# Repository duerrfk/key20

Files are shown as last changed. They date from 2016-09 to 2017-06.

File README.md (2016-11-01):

# What is Key 2.0?

Key 2.0 (or Key20 for short) is a Bluetooth IoT Door Lock controller. It turns a conventional electric door lock into a smart door lock that can be opened using a smartphone without the need for a physical key. Thus, Key20 is the modern version of a physical key, or, as the name suggests, the key version 2.0 for the Internet of Things (IoT) era.

Key20 consists of two parts:

1. Key20 door lock controller device, which is physically connected to the electric door lock and wirelessly via BLE to the mobile app.
2. Key20 mobile app implementing the user interface to unlock the door and communicating with the door lock controller through BLE.

```
         [ Mobile Phone w/ ]
         [    Key20 App    ]
               |
               | Bluetooth Low Energy (BLE) Connection
               |
 |---[ Key20 Door Lock Controller ]---[ Electric Door Lock ]---|
 |   [           Device           ]                            |
 |                                                             |
 |                                                             |
 |                                                             |
 |----------------------(Voltage Source)-----------------------|
                        (    12 VAC    )
```

The following image shows the Key20 door lock controller device and the Key20 app running on a smartphone.

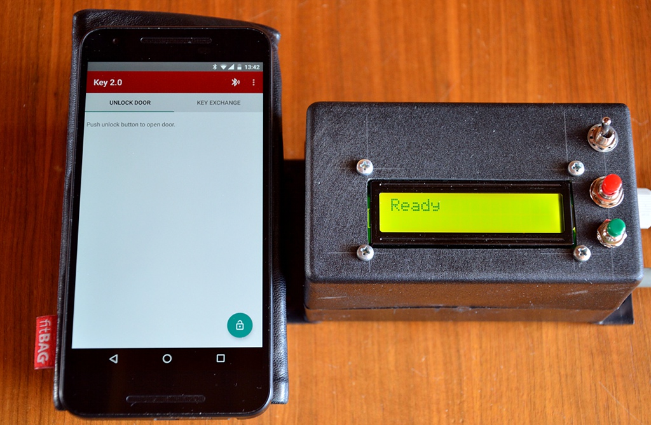
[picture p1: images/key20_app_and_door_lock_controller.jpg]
Key 2.0 Door Lock Controller and App


You can get a quick impression on how Key20 works watching the following video:

[Key 2.0 Video](https://youtu.be/0vUUZOasrV8)

The main features of Key20 are:

* Using state-of-the-art security mechanisms (Elliptic Curve Diffie-Hellman Key Exchange (ECDH), HMAC) to protect against attacks. 
* Open-source software and hardware, including an open implementation of the security mechanisms. No security by obscurity! Source code for the app and door lock controller as well as Eagle files (schematic and board layout) are provided.
* Maker-friendly: using easily available cheap standard components (nRF51822 BLE chip, standard electronic parts), easy to manufacture circuit board, and open-source software and hardware design.
* Works with BLE-enabled Android 4.3 mobile devices (and of course newer versions). Porting to other mobile operating systems like iOS should be straightforward.
* Liberal licensing of software and hardware under the Apache License 2.0 and the CERN Open Hardware License 1.0, respectively.

# Security Concepts

A door lock obviously requires security mechanisms to protect from unauthorized requests to open the door. To this end, Key20 implements the following state of the art security mechanisms.

## Authorization of Door Open Requests with HMAC

All door open requests are authorized through a Keyed Hash Message Authentication Code (HMAC). A 16 byte nonce (big random number) is generated by the door lock controller for each door open request as soon as a BLE connection is made to the door lock controller. The nonce is sent to the mobile app. Both, the nonce and the shared secret, are used by the mobile app to calculate a 512 bit HMAC using the SHA-2 hashing algorithm, which is then truncated to 256 bits (HMAC512-256), and sent to the door lock controller. The door lock controller also calculates an HMAC based on the nonce and the shared secret, and only if both HMACs match, the door will be opened. 

The nonce is only valid for one door open request and effectively prevents replay attacks, i.e., an attacker sniffing on the radio channel and replaying the sniffed HMAC later. Note that the BLE radio communication is not encrypted, and it actually does not need to be encrypted since a captured HMAC is useless when re-played. 

Moreover, each nonce is only valid for 15 s to prevent man-in-the-middle attacks where an attacker intercepts the HMAC and does not forward it immediatelly but waits until the (authorized) user walks away after he is not able to open the door. Later the attacker would then send the HMAC to the door lock controller to open the door. With a time window of only 15 s (which could be reduced further), such attacks are futile since the authorized user will still be at the door.

Note that the whole authentication procedure does not include heavy-weight asymmetric crypto functions, but only light-weight hashing algorithms, which can be performed on the door lock device featuring an nRF51822 micro-controller (ARM Cortex M0) very fast in order not to delay door unlocking. 

With respect to the random nonce we would like to note the following. First, the nRF51822 chip includes a random number generator for generating random numbers from thermal noise, so nonces should be of high quality, i.e., truly random. An attack by cooling down the Bluetooth chip to reduce randomness due to thermal noise is not relevant here since this requires physical access to the lock controller installed within the building, i.e., the attacker is then already in your house.

Secondly, 128 bit nonces provide reasonable security for our purpose. Assume one door open request per millisecond (very pessimistic assumption!) and 100 years of operation, i.e., less than n = 2^42 requests to be protected. With 128 bit nonces, we have m = 2^128 possible nonce values. Then the birthday paradox can be used to calculate the probability p of at least one pair of requests sharing the same nonce, or, inversely, no nonces shared by any pair of requests. An approximation of p for n << m is p(n,m) = 1 - e^((-n^2)/(2*m)), which practically evaluates to 0 for n = 2^42 and m = 2^128. Even for n = 2^52 (one request per us; actually not possible with BLE), p(2^52,2^128) < 3e-8, which is about the probability to be hit by lightning, which is about 5.5e-8.

## Exchanging Keys with Elliptic Curve Diffie Hellman Key Exchange (ECDH)

Obviously, the critical part is the establishment of a shared secret between the door lock controller and the mobile app. Anybody in possession of the shared secret can enter the building, thus, we must ensure that only the lock controller and the Key20 app know the secret. To this end, we use Elliptic Curve Diffie-Hellman (ECDH) key exchange based on Curve 25519. We assume that the door lock controller is installed inside the building that is secured by the lock---if the attacker is already in your home, the door lock is futile anyway. Thus, only the authorized user (owner of the building) has physical access to the door lock controller. 

First, the user needs to press a button on the door lock controller device to enter key exchange mode (the red button in the pictures). Then both, the mobile app and the door lock controller calculate different key pairs based on the Elliptic Curve 25519 and exchange their public keys, which anyone can know. Using the public key of the other party and their own private keys, the lock controller and the app can calculate the same shared secret. 

Using Curve 25519 and the Curve 25519 assembler implementation optimized for ARM Cortex-M0 from the Micro NaCl project, key pairs and shared secrets can be calculated in sub-seconds on the nRF51822 BLE chip (ARM Cortex M0). 

Without further measures, DH is susceptible to man-in-the-middle attacks where an attacker actively manipulates the communication between mobile app and door lock controller. With such attacks, the attacker could exchange his own public key with both, the lock controller and the app to establish two shared secrets between him and the door lock controller, and between him and the mobile app. We prevent such attacks with the following mechanism. After key exchange, the mobile app and the door lock device both display a checksum (hash) of their version of the exchanged shared secret. The user will visually check these checksums to verify that they are the same. If they are the same, no man-in-the-middle attack has happened since the man in the middle cannot calculate the same shared secret as the door lock controller and the mobile app (after all, the private keys of door lock controller and mobile app remain private). Only then the user will confirm the key by pressing buttons on the door lock controller and the mobile app. Remember that only the authorized user has physical access to the door lock controller since it is installed within the building to be secured by the lock. 

The following image shows the mobile app and the door lock controller displaying a shared secret checksum after key exchange. The user can confirm this secret by pushing the green button the the lock controller device and the Confirm Key button of the app.

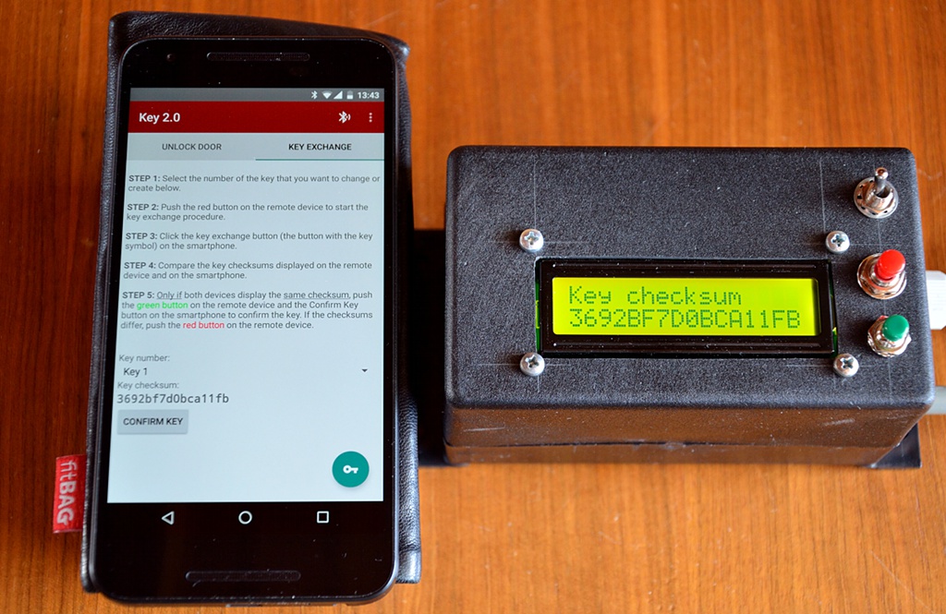
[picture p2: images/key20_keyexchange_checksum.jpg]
Key Exchange with Checksum

 
## Why not Standard Bluetooth Security?

Actually, Bluetooth 4.2 implements security concepts similar to the mechanisms described above. So it is a valid question why don't we just rely on the security concepts implemented by Bluetooth?

A good overview why Bluetooth might not be as secure as we would like it to be is provided by [Francisco Corella](https://pomcor.com/2015/06/03/has-bluetooth-become-secure/). So we refer the interested reader to his page for the technical details and a discussion of Bluetooth security. We also would like to add that many mobile devices still do not implement Bluetooth 4.2 but only Bluetooth 4.0, which is even less secure than Bluetooth 4.2.

So we decided not to rely on Bluetooth security mechanisms, but rather implement all security protocols on the application layer using state of the art security mechanisms as described above.

# Bluetooth Door Lock Controller Device

The Door Lock Controller Device needs to be connected to the electric door lock (2 cables). You can simply replace a manual switch by the door lock controller device. 

The door lock controller needs to be placed in Bluetooth radio range to the door and inside the building. Typical radio ranges are about 10 m. Depending on the walls, the distance might be shorter or longer. In our experience, one concrete wall is no problem, but two might block the radio signal.  

## Door Lock Controller Hardware

The door lock controller hardware is designed for operating AC (alternating current) electric door locks, which typically run from 6-12 VAC. 

The hardware design (schematics and board layout for Eagle) for the door lock controller device can be found in folder `pcb/key20-ble`. 

The following images show the hardware and schematic. The hardware basically concists of one circuit board (PCB). We deliberately used a simple single-sided through-hole design to help makers producing their own boards. An LCD, a power switch, and two push buttons for user interaction are connected to the main PCB. An ob-board voltage regulator provides 3.3 V fed by an external DC power supply (anything between 4 V and 30 V will work). The circuit draws less than 50 mA when the lock is operated, thus, you can use a cheap 5.0 V USB power supply. With a little modification, we could also switch off the LCD when not needed, and the device could run from 4 AA-size batteries most probably for years.

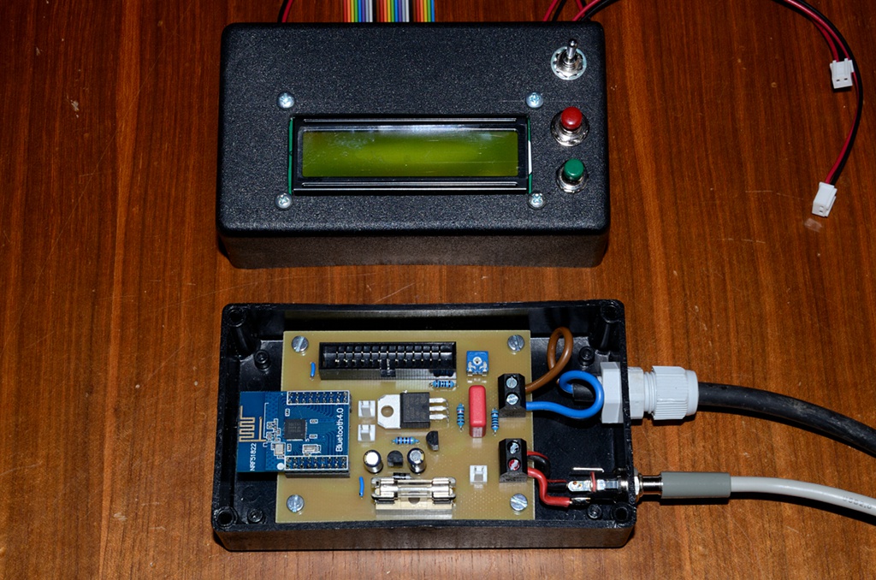
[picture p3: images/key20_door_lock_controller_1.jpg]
Key 2.0 PCB and LCD

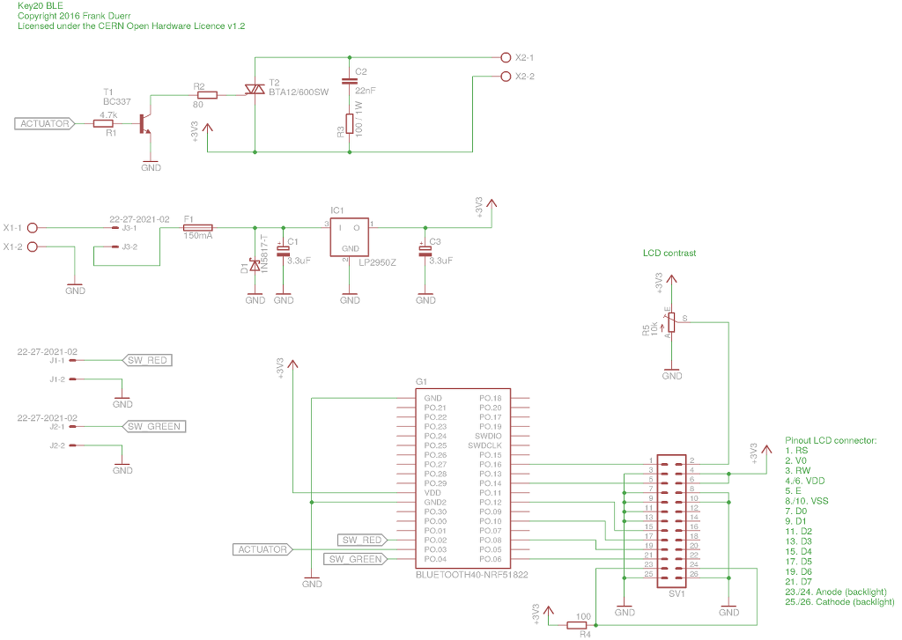
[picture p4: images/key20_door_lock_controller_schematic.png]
Key 2.0 Schematic


The main part of the hardware is an nRF51822 BLE chip from Nordic Semiconductors. You can buy so-called "Bluetooth 4.0" breakout boards with an nRF51822 (version 3, variant AA w/ 16 kB of RAM and 256 kB flash memory) and two 2x9 connectors (2 mm pitch) for about 6 US$ including shipping. To connect the Bluetooth 4.0 board hosting the nRF51822, the PCB has two 2x9 pin connectors (no SMD soldering required). The nRF51822 features an ARM Cortex M0 micro-controller and a so-called softdevice implementing the Bluetooth stack, which runs together with the application logic on the ARM Cortex M0 processor. Key20 uses the S110 softdevice version 8.0 (see next sub-section on how to flash the softdevice and the Key20 application code). 

The nRF51822 operates the electric door lock through a TRIAC. Note that most electric door locks use alternating current (AC), so a transistor will not work. We have added a snubber circuit (capacitor and resistor) to drive the inductive load (electric door lock) since TRIACs are sensitive to sudden voltage jumps possibly leading to unwanted turn-on, i.e., door unlocking. The TRIAC is operated in quadrant 2 and 3 (current flowing out of the gate) to avoid the less sensitive quadrant 4. Since the TRIAC needs about 30 mA to trigger reliably, a transistor is used to drive the TRIAC by the nRF51822, reducing the current on the micro-controller's GPIO to less than 1 mA.

Note that our design is targeting electric door locks using small AC voltages (typically 6-12 V AC). Theoretically, the TRIAC can drive 230 V loads up to 16 A. However, for safe 230 V and higer current operation the design has to be adapted, e.g., X2 snubber capacitor, isolation of the low-voltage part (3.3 V microcontroller) from the 230 V part through an opto-TRIAC, larger trace width and distances, etc. 

An LCD is used to implement the secure key exchange procedure described above (visual key verification to avoid man-in-the-middle attacks). We used a common HD44780-compatible LCD display with 2x16 characters (1602A, 2-3 US$ including shipping). The LCD is connected to the main PCB through a ribbon cable. We designed a custom adapter board for connecting and mounting the 1602A LCD (see folder `pcb/lcd1602a-connector`).

## Lock Controller Software

### Overview

The software for the door lock controller can be found in folder `nrf51`.

Keys (shared secrets) are persistently stored in flash. Currently, we store 4 keys, but you can easily increase this number up to the limit of the flash size (nRF51822 version 3, variant AA comes with 256 kB flash, and each key consumes only 32 bytes).  

Application events and a state machine approach are used to implement the application logic. Events are handled outside the interrupt context to avoid blocking the softdevice. In particular, actions like calculating keys or hashes can take significant time, although the crypto implementations used by Key20 can also process such compute-heavy tasks in just hundreds of milliseconds.   

A lean-and-mean library was implemented for the nRF51822 chip to drive the LCD. 

For more details, please have a look at the source code.

### Prerequisites for Building the Software

No heavy-weight IDE is required to build the code. However, still a few tools are required to build and flash the code (tested with the given version numbers):

* [nRF51 SDK, version 10.0.0](http://developer.nordicsemi.com/nRF5_SDK/)
* [nRF5x Command Line Tools, version 8.2.0](https://www.nordicsemi.com/eng/Products/nRF51-DK)
* [Softdevice S110, version 8.0.0](https://www.nordicsemi.com/eng/Products/nRF51-DK)
* Flashing and debugging hardware, e.g., [Segger J-Link EDU](https://www.segger.com/j-link-edu.html) (about 50 US$, only for non-commerical use!). The nRF51 Developers Kit (DK) comes with an on-board Segger programmer, but for flashing the Key20 board, you need an external programmer like the J-Link EDU. 
* [Tool chain (compiler, linker, etc.) for ARM](https://launchpad.net/gcc-arm-embedded/+download)

### Building and Flashing the Software

First, adapt the Makefile by defining the following variables:

* `NRF51_SDK`: path to the nRF51 SDK directory
* `CROSS`: path to the compiler tools
* `CFLAGS`: add `-DTARGET_BOARD_NRF51DK` if you compile for the nRF51 Development Kit (DK); if this definition is not set, you compile for the Key20 board.
* `LINKER_SCRIPT`: set to `nrf51422_ac_s110.ld` for the nRF51 DK (nRF51422, variant AC) or to `nrf51822_aa_s110.ld` for the Key20 board (nRF51822, variant AA).

Compiling the code:

```
$ cd nrf51
$ make
```

Flashing the softdevice:

```
$ nrfjprog --family NRF51 --program s110_nrf51_8.0.0_softdevice.hex --chiperase --verify
```

Flashing the application:

```
nrfjprog --family NRF51 --program key20.hex --verify --sectorerase
```

Rebooting after flashing:

```
nrfjprog -r
```

# Android App

The source code of the Key20 app for Android can be found in folder `android/Key20`. The code was developed with Android Studio 2.1.

The app requires a BLE-enabled mobile device running Android version 4.3 "Jelly Bean" (API level 18) or higher. 

The following images show the two major tabs of the app: one for opening the door, and the second for exchanging keys between the app and the door lock controller.

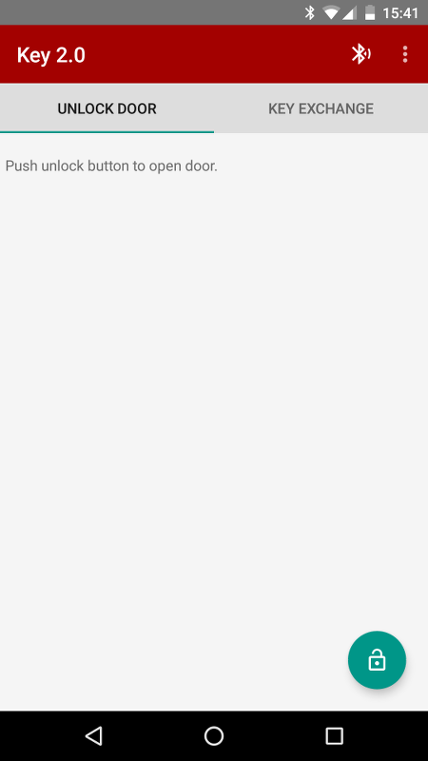
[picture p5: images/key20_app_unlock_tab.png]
Key 2.0 App: Unlock Tab


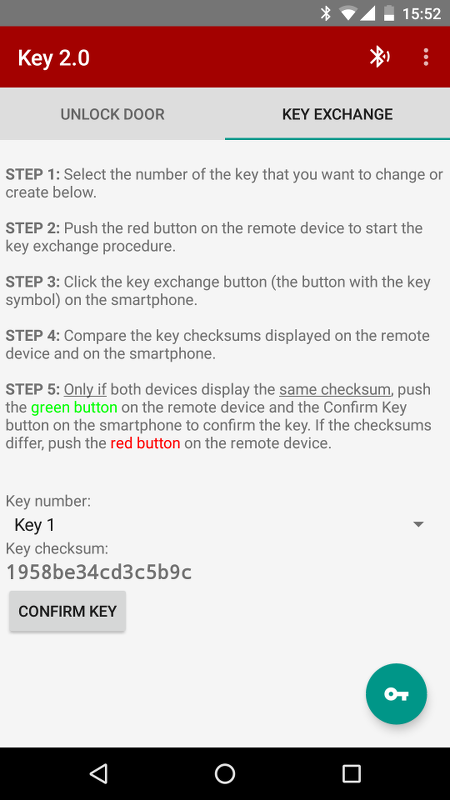
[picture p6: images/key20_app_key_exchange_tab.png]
Key 2.0 App: Key Exchange Tab


# License and Acknowledgments

The Key20 software (contents of folders `nrf51` and `android`) is licensed under the Apache License, Version 2.0.

The Key20 hardware documentation (contents of folder `pcb`) is licensed under the CERN Open Hardware Licence, Version 1.2

Both licenses are included in the repository in the files `LICENSE-SOFTWARE` and `LICENSE-HARDWARE`, respectively.

Key20 uses the Micro-NaCl crypto library, specifically, AVRNaCl (folder `avrnacl`) by Michael Hutter and Peter Schwabe, and M0NaCl  (folder `curve25519-cortexm0`) by Björn Haase and Ana Helena Sánchez. The authors have released Micro-NaCl to the public domain, and we gratefully acknowledge their generous contribution.

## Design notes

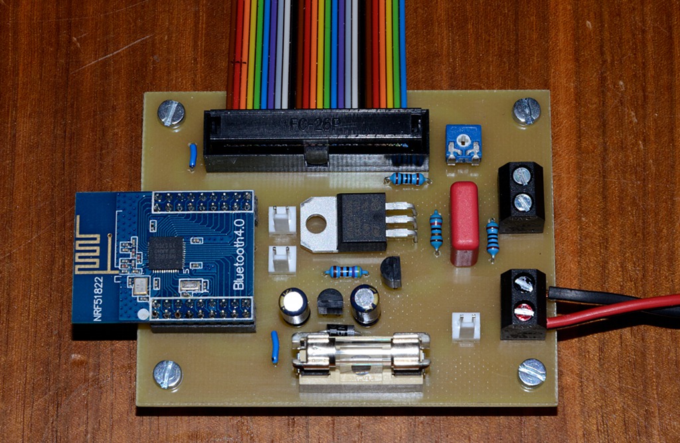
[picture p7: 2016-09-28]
images/key20_door_lock_controller_2.jpg

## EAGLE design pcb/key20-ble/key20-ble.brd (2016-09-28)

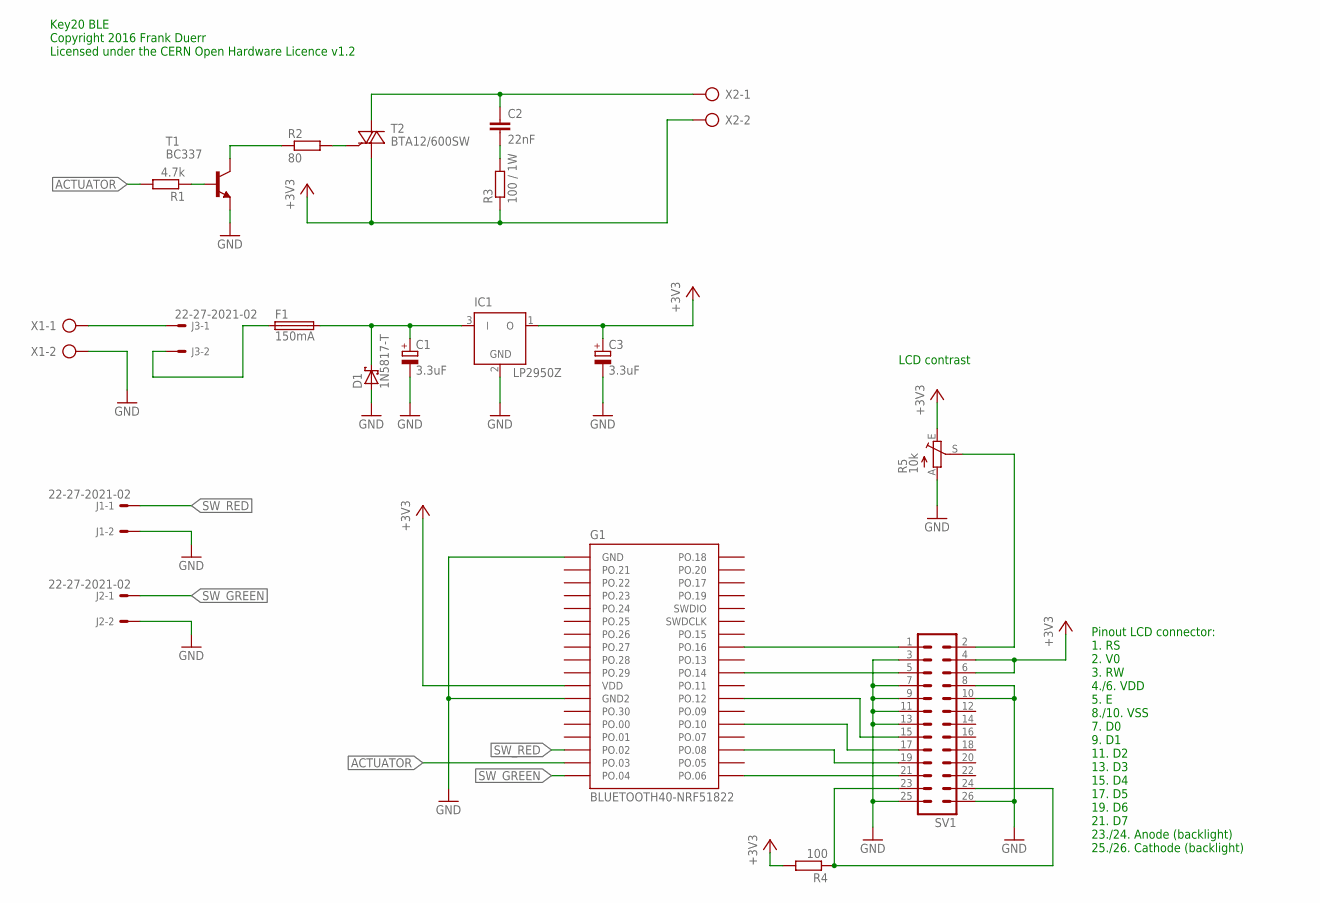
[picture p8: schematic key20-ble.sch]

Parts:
C1, C3: 3.3uF; E2,5-5
C2: 22nF; C102-054X133
D1: 1N5817-T; DO41-7.6
F1: 150mA; SH22,5
G1: BLUETOOTH40-NRF51822; BLUETOOTH40-NR51822
IC1: LP2950Z; TO92
J1, J2, J3: 22-27-2021-02; 6410-02
R1: 4.7k; 0207/7
R2: 80; 0207/7
R3: 100 / 1W; 0207/7
R4: 100; 0207/7
R5: 10k; CA6V
SV1: ML26
T1: BC337; TO92
T2: BTA12/600SW; TO220BV
X1, X2: AK500/2

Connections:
+3V3: C3.+, G1.VDD, IC1.1 (O), R3.1, R4.2, R5.E, SV1.4, SV1.6, T2.T1 (A1), X2.2
ACTUATOR: G1.PO.03, R1.2
GND: C1.-, C3.-, D1.A, G1.GND, G1.GND2, IC1.2 (GND), J1.2, J2.2, R5.A, SV1.3, SV1.7, SV1.8, SV1.9, SV1.10, SV1.11, SV1.13, SV1.25, SV1.26, T1.1 (E), X1.2
unnamed: R2.2, T2.G
unnamed: C2.2, R3.2
unnamed: C2.1, T2.T2 (A2), X2.1
unnamed: R1.1, T1.2 (B)
unnamed: R2.1, T1.3 (C)
unnamed: G1.PO.08, SV1.19
unnamed: F1.1, J3.2
unnamed: G1.PO.06, SV1.21
unnamed: G1.PO.14, SV1.5
unnamed: G1.PO.16, SV1.1
unnamed: R5.S, SV1.2
unnamed: R4.1, SV1.23, SV1.24
unnamed: J3.1, X1.1
unnamed: C1.+, D1.C, F1.2, IC1.3 (I)
unnamed: G1.PO.10, SV1.17
unnamed: G1.PO.12, SV1.15
SW_GREEN: G1.PO.04, J2.1
SW_RED: G1.PO.02, J1.1

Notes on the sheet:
Pinout LCD connector: 1. RS 2. V0 3. RW 4./6. VDD 5. E 8./10. VSS 7. D0 9. D1 11. D2 13. D3 15. D4 17. D5 19. D6 21. D7 23./24. Anode (backlight) 25./26. Cathode (backlight)
LCD contrast
Key20 BLE Copyright 2016 Frank Duerr Licensed under the CERN Open Hardware Licence v1.2

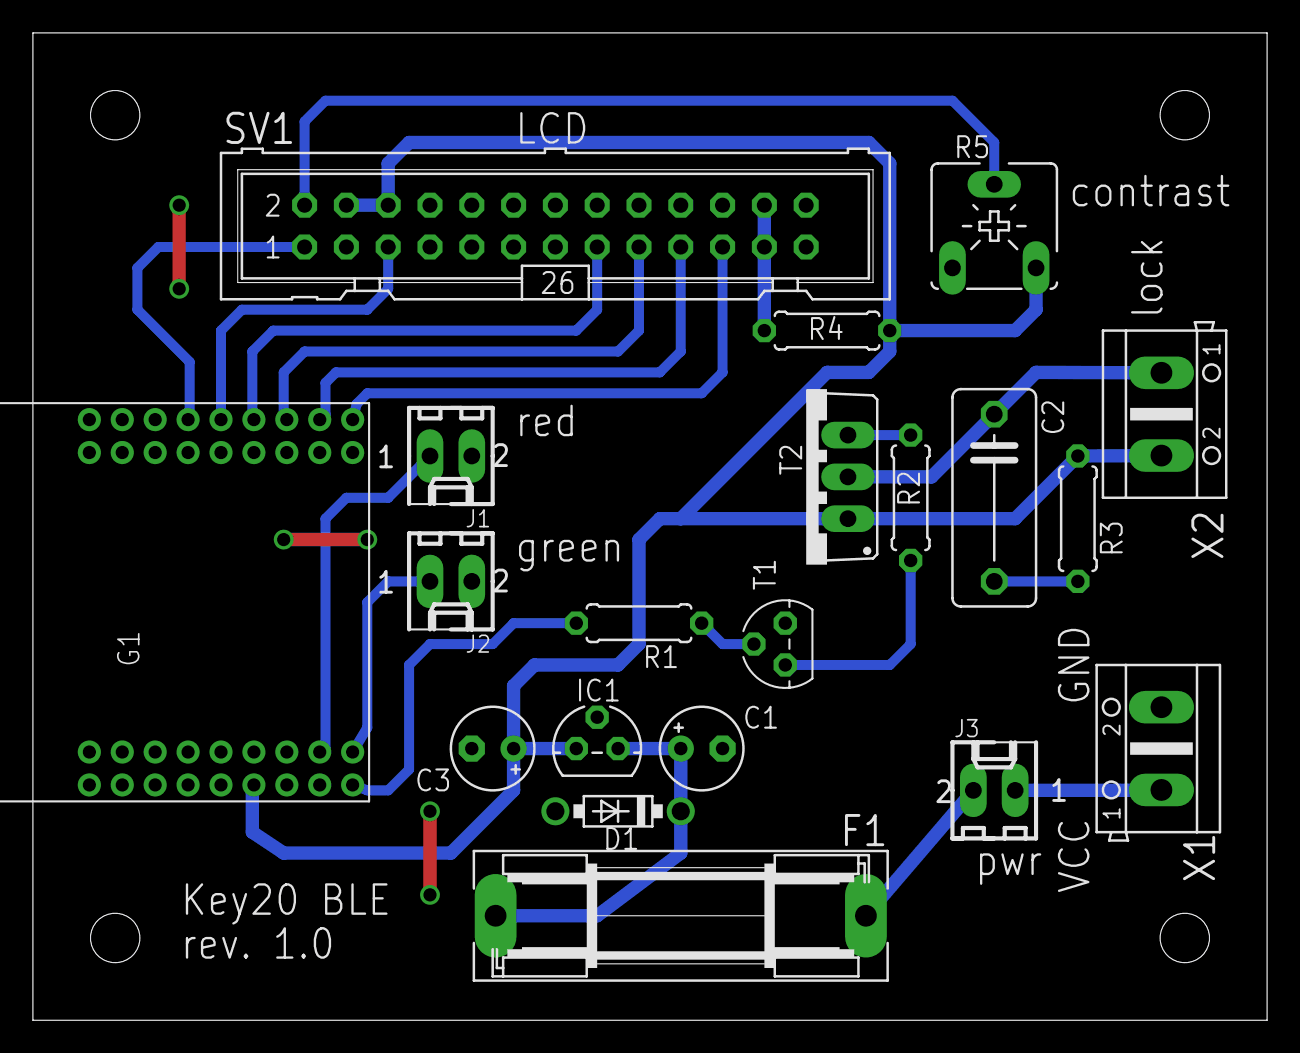
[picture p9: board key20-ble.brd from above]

Board: 2 copper layers, 75.0 x 60.0 mm, 20 parts (0 on the bottom side), 21 nets.

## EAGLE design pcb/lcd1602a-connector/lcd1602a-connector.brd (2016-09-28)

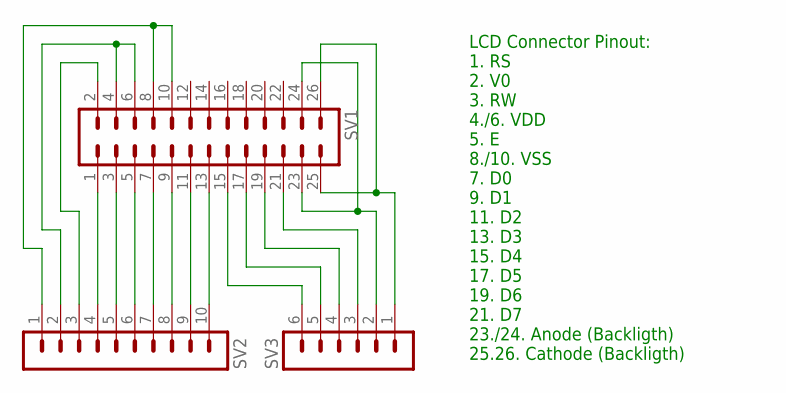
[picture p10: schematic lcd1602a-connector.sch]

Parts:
SV1: ML26
SV2: MA10-1
SV3: MA06-1

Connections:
unnamed: SV1.1, SV2.4
unnamed: SV1.3, SV2.5
unnamed: SV1.5, SV2.6
unnamed: SV1.7, SV2.7
unnamed: SV1.9, SV2.8
unnamed: SV1.11, SV2.9
unnamed: SV1.13, SV2.10
unnamed: SV1.15, SV3.6
unnamed: SV1.17, SV3.5
unnamed: SV1.21, SV3.3
unnamed: SV1.23, SV1.24, SV3.2
unnamed: SV1.19, SV3.4
unnamed: SV1.25, SV1.26, SV3.1
unnamed: SV1.2, SV2.3
unnamed: SV1.4, SV1.6, SV2.2
unnamed: SV1.8, SV1.10, SV2.1

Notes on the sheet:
LCD Connector Pinout: 1. RS 2. V0 3. RW 4./6. VDD 5. E 8./10. VSS 7. D0 9. D1 11. D2 13. D3 15. D4 17. D5 19. D6 21. D7 23./24. Anode (Backligth) 25.26. Cathode (Backligth)

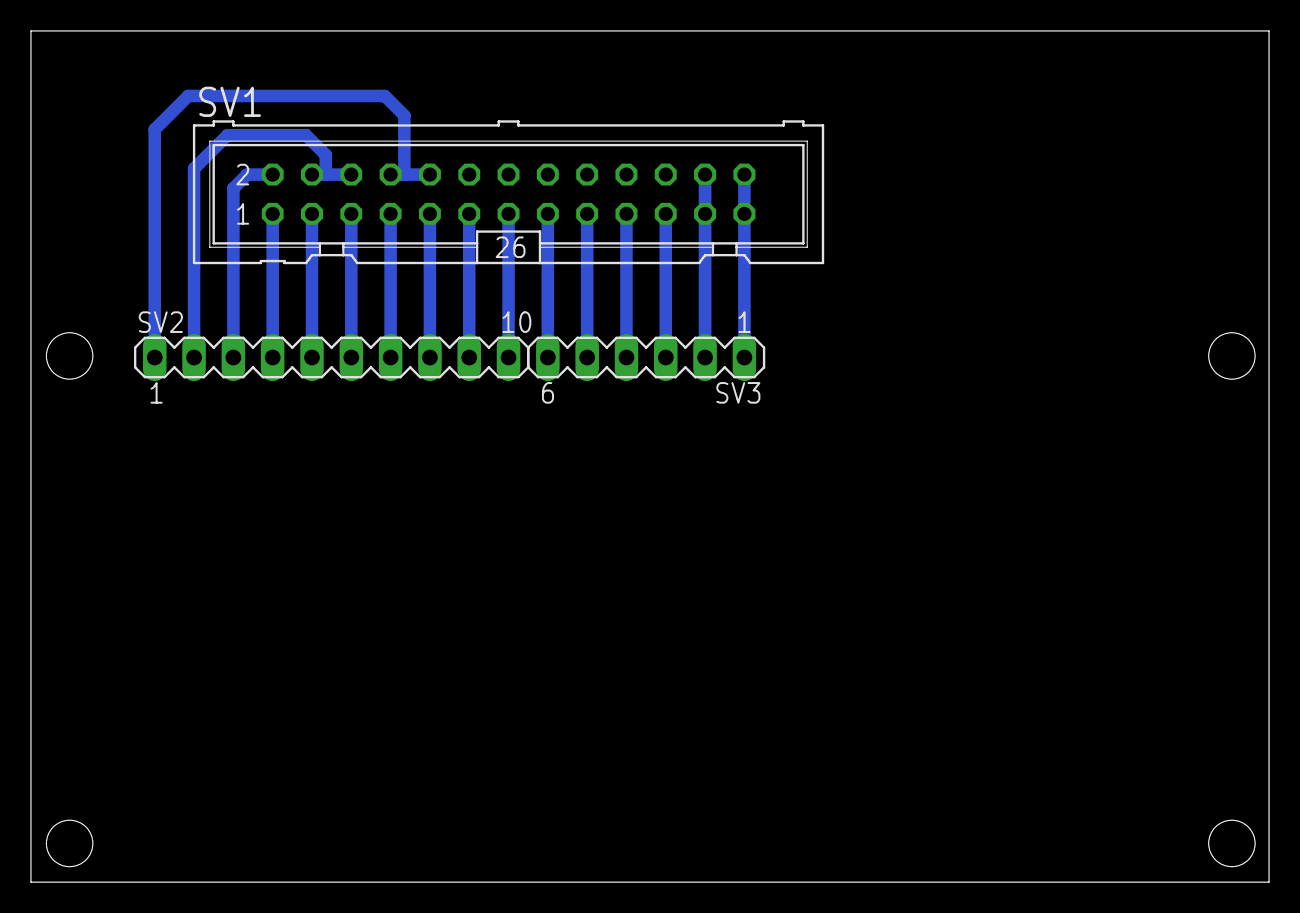
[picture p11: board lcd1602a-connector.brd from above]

Board: 2 copper layers, 80.0 x 55.0 mm, 3 parts (0 on the bottom side), 16 nets.

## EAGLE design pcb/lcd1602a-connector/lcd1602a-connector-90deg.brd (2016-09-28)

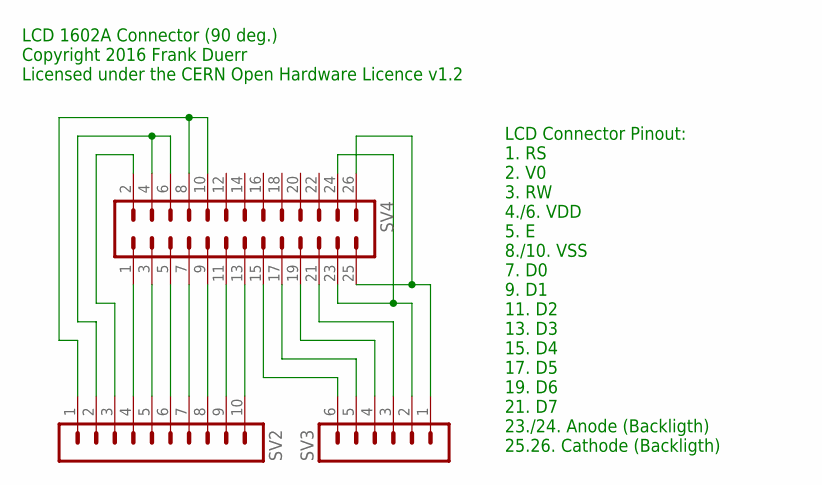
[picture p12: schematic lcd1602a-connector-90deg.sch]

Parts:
SV2: MA10-1
SV3: MA06-1
SV4: ML26L

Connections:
unnamed: SV2.4, SV4.1
unnamed: SV2.5, SV4.3
unnamed: SV2.6, SV4.5
unnamed: SV2.7, SV4.7
unnamed: SV2.8, SV4.9
unnamed: SV2.9, SV4.11
unnamed: SV2.10, SV4.13
unnamed: SV3.6, SV4.15
unnamed: SV3.5, SV4.17
unnamed: SV3.3, SV4.21
unnamed: SV3.2, SV4.23, SV4.24
unnamed: SV3.4, SV4.19
unnamed: SV3.1, SV4.25, SV4.26
unnamed: SV2.3, SV4.2
unnamed: SV2.2, SV4.4, SV4.6
unnamed: SV2.1, SV4.8, SV4.10

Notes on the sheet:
LCD Connector Pinout: 1. RS 2. V0 3. RW 4./6. VDD 5. E 8./10. VSS 7. D0 9. D1 11. D2 13. D3 15. D4 17. D5 19. D6 21. D7 23./24. Anode (Backligth) 25.26. Cathode (Backligth)
LCD 1602A Connector (90 deg.) Copyright 2016 Frank Duerr Licensed under the CERN Open Hardware Licence v1.2

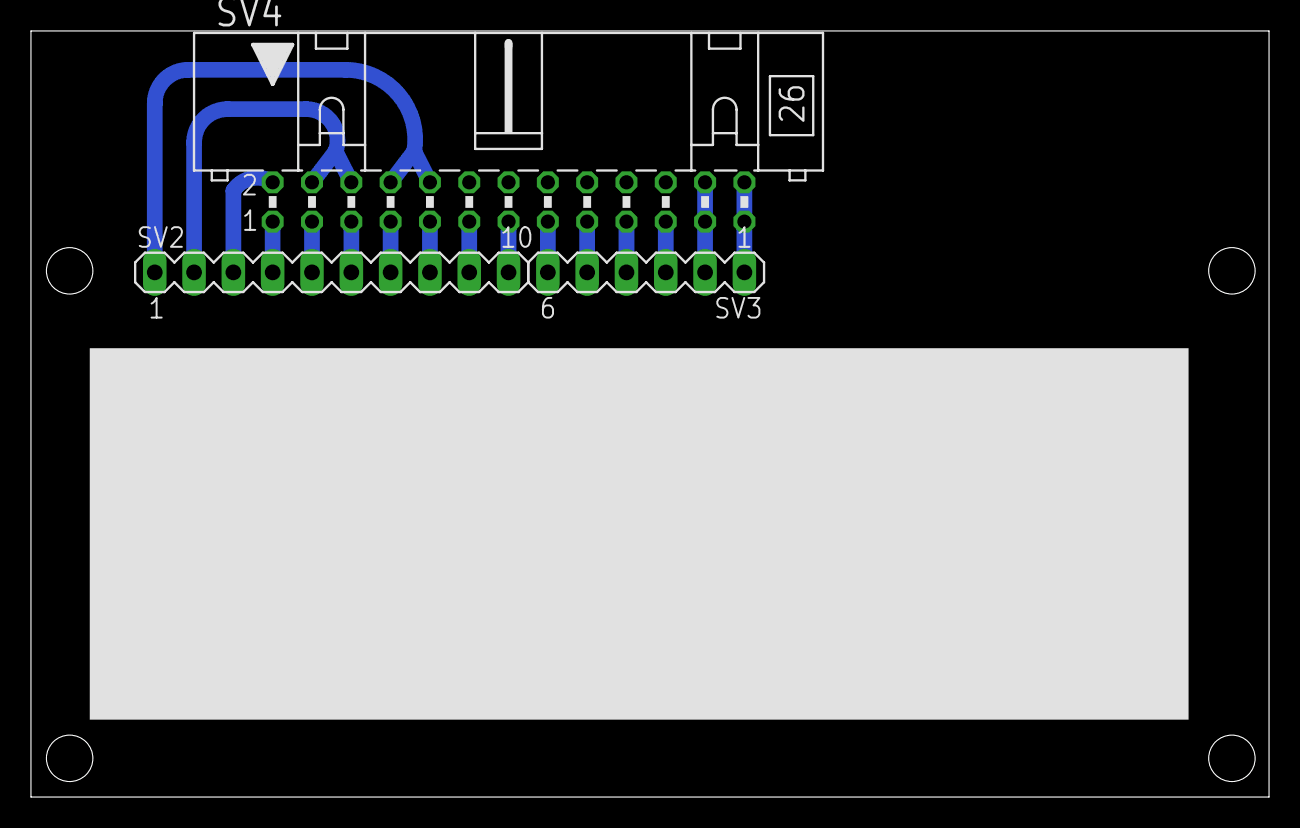
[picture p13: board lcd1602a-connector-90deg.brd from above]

Board: 2 copper layers, 80.0 x 49.5 mm, 3 parts (0 on the bottom side), 16 nets.

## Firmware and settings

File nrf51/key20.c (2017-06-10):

/**
 * This file is part of Key20.
 *
 * Copyright 2016 Frank Duerr
 *
 * Licensed under the Apache License, Version 2.0 (the "License");
 * you may not use this file except in compliance with the License.
 * You may obtain a copy of the License at
 * 
 * http://www.apache.org/licenses/LICENSE-2.0
 * 
 * Unless required by applicable law or agreed to in writing, software
 * distributed under the License is distributed on an "AS IS" BASIS,
 * WITHOUT WARRANTIES OR CONDITIONS OF ANY KIND, either express or implied.
 * See the License for the specific language governing permissions and
 * limitations under the License.
 */

#include <string.h>
#include <nrf.h>
#include <nrf_gpio.h>
#include <ble.h>
#include <softdevice_handler.h>
#include <ble_advdata.h>
#include <app_timer.h>
#include <app_button.h>
#include <pstorage.h>
#include <curve25519-cortexm0.h>
#include <avrnacl.h>
#include <hd44780nrf51.h>
#include <ble_hci.h>
#include "app_event_queue.h"

// Pinout of development board (DK):
// * Pin 17: Button 1
// * Pin 18: Button 2 
// * Pin 21: LED 1
// * Pin 22: LED 2
#ifdef TARGET_BOARD_NRF51DK
#define PIN_BUTTON_RED 17
#define PIN_BUTTON_GREEN 18
#define PIN_LOCK 22
#define PIN_LED 21
#define PIN_LCD_RS 16
#define PIN_LCD_E 19
#define PIN_LCD_DB4 12
#define PIN_LCD_DB5 13
#define PIN_LCD_DB6 14
#define PIN_LCD_DB7 15
#else
// Pinout of Key20 lock controller board:
#define PIN_BUTTON_RED 2
#define PIN_BUTTON_GREEN 4
#define PIN_LOCK 3
// Actually, the Key20 board has no LED.
// Pin 21 is not connected on this board, so it will also do no harm.
#define PIN_LED 21
#define PIN_LCD_RS 16
#define PIN_LCD_E 14
#define PIN_LCD_DB4 12
#define PIN_LCD_DB5 10
#define PIN_LCD_DB6 8
#define PIN_LCD_DB7 6
#endif

// Maximum number of pending application events. 
// In order to decouple event processing from event generation happening
// in the context of interrupts, we use an application event queue.
// Application events are then processed outside the interrupt context.
#define APP_EVENT_QUEUE_SIZE 16

// Number of keys.
#define KEY_COUNT 4

// Application-level events.
#define APP_EVENT_AUTH_TIMEOUT 0
#define APP_EVENT_BUTTON_RED_PRESSED 1
#define APP_EVENT_BUTTON_GREEN_PRESSED 2
#define APP_EVENT_CLIENT_CONNECTED 3
#define APP_EVENT_CLIENT_DISCONNECTED 4
#define APP_EVENT_SUBSCRIBED_CFG_OUT 5
#define APP_EVENT_SUBSCRIBED_NONCE 6
#define APP_EVENT_KEY_PART_RCVD 7
#define APP_EVENT_HMAC_PART_RCVD 8
#define APP_EVENT_PSTORE_READY 9
#define APP_EVENT_LOCK_ACTION_TIMEOUT 10
#define APP_EVENT_INDICATION_NONCE_RCVD 11
#define APP_EVENT_INDICATION_CFG_OUT_RCVD 12

// Length of Diffie-Hellman keys using Eliptic Curve 25519 [bytes].
#define ECDH_KEY_LENGTH crypto_scalarmult_curve25519_BYTES

// Length of a SHAR512 [bytes].
#define SHA512_HASH_LENGTH crypto_hash_sha512_BYTES

// Length of an HMAC512-256 [bytes].
#define HMAC512_256 crypto_auth_hmacsha512256_BYTES

// Max. length of the Nonce characteristic.
#define MAX_LENGTH_NONCE_CHAR 16
 
// Max. length of Unlock characteristic [bytes].
#define MAX_LENGTH_UNLOCK_CHAR 18

// Max. length of config-in characteristic [bytes].
#define MAX_LENGTH_CFG_IN_CHAR 18

// Max. length of config-out characteristic [bytes].
#define MAX_LENGTH_CFG_OUT_CHAR 18

// Length of nonces used to avoid replay attacks [bytes].
// 128 bit nonces provide for sufficient security, assuming the following
// parameters:
// 
// 1. one request per millisecond and 100 years of operation 
//    -> less than n = 2**42 requests to protect.
// 2. m = 2**128 different nonces.
//
// Then the birthday paradox can be used to calculate the probability p of 
// at least one pair of requests sharing the same nonce, or, inversely,
// no nonces shared by any pair of requests. An approximation of p for n << m 
// is p(n,m) = 1 - e**((-n**2)/(2*m)), which practically evaluates to 0 for
// n = 2**42 and m = 2**128. Even for n = 2**52 (one request per us), 
// p(2**52,2**128) < 3e-8 which is about the probability to be hit by 
// lightning (about 5.5e-8).
// A nonce of 16 bytes also fits nicely into a characteristic.
#define NONCE_LENGTH 16

#define DEVICE_NAME "Key20"
// Minimum connection interval in 1.25 ms. Minimum allowed value: 7.5 ms.
// 16 -> 20 ms.
#define MIN_CONN_INTERVAL 16
// Maximum connection interval in 1.25 ms. Maximum allowed value: 4000 ms.
// 100 -> 125 ms.
#define MAX_CONN_INTERVAL 100
// Number of connection intervals the device can stay silent.
#define SLAVE_LATENCY 2
// Connection supervision timeout, i.e., time until a link is considered
// lost, in 10 ms.
// 400 -> 4 s. 
#define CONN_SUP_TIMEOUT 400
// Advertisement interval in 0.625 ms; min. 20 ms, max 10.24 s.
// 64 -> 40 ms.
#define ADV_INTERVAL 64
// How long to advertise in seconds (0 = forever)
#define ADV_TIMEOUT 0

// Prescaler of RTC1 (low-frequency clock at 32.768 kHz), which is used by the 
// app timer (RTC0 is used by the softdevice, and, therefore, cannot be used by 
// the application). 
#define APP_TIMER_PRESCALER 0
#define APP_TIMER_QUEUE_SIZE 6

// Delay for debouncing buttons [ms].
#define BUTTON_DETECTION_DELAY APP_TIMER_TICKS(50, APP_TIMER_PRESCALER)

// Authentication timeout [ms].
#define AUTH_TIMER_TIMEOUT APP_TIMER_TICKS(10000, APP_TIMER_PRESCALER)

// Time for operating the lock [ms].
#define LOCK_ACTION_TIMER_TIMEOUT APP_TIMER_TICKS(2000, APP_TIMER_PRESCALER)

// Service and charateristic UUIDs in Little Endian format.
// The 16 bit values will become byte 12 and 13 of the 128 bit UUID:
// 0x0a9dXXXX-5ff4-4c58-8a53627de7cf1faf
#define UUID_BASE {0xaf, 0x1f, 0xcf, 0xe7, 0x7d, 0x62, 0x53, 0x8a, \
	           0x58, 0x4c, 0xf4, 0x5f, 0x00, 0x00, 0x9d, 0x0a}
#define UUID_SERVICE 0x0001
#define UUID_CHARACTERISTIC_NONCE 0x0002
#define UUID_CHARACTERISTIC_UNLOCK 0x0003
#define UUID_CHARACTERISTIC_CFG_IN 0x0004
#define UUID_CHARACTERISTIC_CFG_OUT 0x0005

// Application states.
enum app_states {idle, cfg_wait_connection, cfg_wait_subscription, 
		 cfg_wait_key_part1, cfg_wait_key_part2, cfg_wait_decision, 
		 auth_wait_hmac_part1, auth_wait_hmac_part2, cfg_wait_key_store, 
		 auth_wait_lock_action_timeout, booting, cfg_wait_disconnect,
		 auth_wait_disconnect, aborted_wait_disconnect, 
		 auth_wait_subscription, auth_wait_nonce_rcvd,
		 cfg_wait_server_key_part1_rcvd, cfg_wait_server_key_part2_rcvd};

enum app_states app_state;

// A valid key store will have this (random) pattern as the first bytes.
// If not, this is an indication that the key store has never been
// written before, thus, there are not valid keys stored, and the
// key store should be initialized ("formatted") first.
// pstore_preamble must be word aligned to be used as memory location for
// pstorage operations.
uint8_t pstore_preamble[] __attribute__((aligned(4))) = 
      {0xfe, 0xec, 0x91, 0xf1, 0x06, 0xc4,
      0x40, 0x24, 0xbf, 0x19, 0x69, 0x7f, 
      0x96, 0x4d, 0xc6, 0x67};

// Definition of the LCD. 
struct hd44780 lcd = {
      .pin_rs = PIN_LCD_RS, 
      .pin_e = PIN_LCD_E, 
      .pin_db4 = PIN_LCD_DB4, 
      .pin_db5 = PIN_LCD_DB5, 
      .pin_db6 = PIN_LCD_DB6,
      .pin_db7 = PIN_LCD_DB7, 
      .rows = 2,
      .columns = 16
};

APP_TIMER_DEF(auth_timer);
APP_TIMER_DEF(lock_action_timer);

// keys variable must be word aligned to be used as memory location for
// pstorage operations.
uint8_t keys[KEY_COUNT][ECDH_KEY_LENGTH] __attribute__((aligned(4)));
// Bitset signaling which keys are valid (key is valid iff bit != 0).
// First key = bit0, second key = bit1, etc.
uint8_t keys_valid = 0;

uint8_t uuid_type;
uint16_t service_handle;
ble_gatts_char_handles_t char_handle_nonce;
ble_gatts_char_handles_t char_handle_unlock;
// The cfg_in characteristic is used for configuration messages from the
// client to the server (this device).
ble_gatts_char_handles_t char_handle_cfg_in;
// The cfg_out characteristic is used for configuration messages from the
// server (this device) to the client.
ble_gatts_char_handles_t char_handle_cfg_out;
uint16_t conn_handle = BLE_CONN_HANDLE_INVALID; 

uint8_t nonce[NONCE_LENGTH];

// During Diffie-Hellman key exchange, we need to keep some temporary keys.
// All keys are stored and transmitted in Little Endian format.
uint8_t keyexchange_server_secret_key[ECDH_KEY_LENGTH];
uint8_t keyexchange_server_public_key[ECDH_KEY_LENGTH];
uint8_t keyexchange_client_public_key[ECDH_KEY_LENGTH];
uint8_t keyexchange_shared_secret[ECDH_KEY_LENGTH];
uint8_t keyexchange_key_no = 0;

// For unlocking, the client has to provide an HMAC and key number.
uint8_t unlock_key_no = 0;
uint8_t unlock_hmac_client[HMAC512_256];

struct app_event_queue app_event_queue;

pstorage_handle_t pstore_handle;
volatile bool is_pstore_ready = false;

// Prototypes.

static void display_text(const char *text1, unsigned int length1,
			 const char *text2, unsigned int length2);
static void set_nonce_char();

// Implementations.

static void led_off()
{
     // LED is active low -> set to turn off.
     nrf_gpio_pin_set(PIN_LED);
}

static void led_on()
{
     // LED is active low -> clear to turn on.
     nrf_gpio_pin_clear(PIN_LED);
}

static void led_init()
{
     nrf_gpio_cfg_output(PIN_LED);
     led_off();
}

/**
 * We follow the "let it crash" paradigm known from Erlang. If something
 * unexpected happens (in particular, an SDK function not returning
 * NRF_SUCCESS), we reboot the system. So "die" actually means, die and
 * be reborn ("self-healing"). Besides that, we of course try to avoid 
 * situations where things might fail (defensive programming). However, 
 * in very unlikely failure situations, we opt for crashing and rebooting 
 * rather than overloading code (and precious code memory) with failure 
 * handling routines.
 */
static void die()
{
     display_text("Error", 5, NULL, 0);
     __disable_irq();
 
     // In a development system, we loop forever.
     // Remove the endless loop in a productive system to auto-reset.
     //while (1);
     
     // In a productive system, we automatically reset the system on errors.
     sd_nvic_SystemReset();
}

static void lock_init()
{
     nrf_gpio_cfg_output(PIN_LOCK);
     // The lock is active high.
     nrf_gpio_pin_clear (PIN_LOCK);
}

static void start_advertising()
{
    uint32_t err_code;
    ble_gap_adv_params_t adv_params;

    memset(&adv_params, 0, sizeof(adv_params));
    adv_params.type = BLE_GAP_ADV_TYPE_ADV_IND;
    adv_params.p_peer_addr = NULL;
    adv_params.fp = BLE_GAP_ADV_FP_ANY;
    adv_params.interval = ADV_INTERVAL;
    adv_params.timeout = ADV_TIMEOUT;

    err_code = sd_ble_gap_adv_start(&adv_params);
    if (err_code != NRF_SUCCESS)
	 die();
}

static void char_cfg_in_write_evt(ble_gatts_evt_write_t *evt_write)
{
     uint8_t key_part_number;
     struct app_event app_event;

     if (evt_write->handle == char_handle_cfg_in.value_handle && 
	 evt_write->len == MAX_LENGTH_CFG_IN_CHAR) {
	  keyexchange_key_no = evt_write->data[0];
	  if (keyexchange_key_no >= KEY_COUNT) {
	       // Invalid key number. 
	       return;
	  }
	  key_part_number = evt_write->data[1];
	  if (key_part_number == 0) 
	       memcpy(keyexchange_client_public_key, 
		      &evt_write->data[2], 16);
	  else
	       memcpy(&keyexchange_client_public_key[16], 
		      &evt_write->data[2], 16);
	  app_event.event_type = APP_EVENT_KEY_PART_RCVD;
	  app_event_queue_add(&app_event_queue, app_event);
     }
}

static void char_unlock_write_evt(ble_gatts_evt_write_t *evt_write)
{
     uint8_t key_part_number;
     struct app_event app_event;
     
     if (evt_write->handle == char_handle_unlock.value_handle && 
	 evt_write->len == MAX_LENGTH_UNLOCK_CHAR) {
	  unlock_key_no = evt_write->data[0];
	  if (unlock_key_no >= KEY_COUNT) {
	       // Invalid key number.
	       return;
	  }
	  key_part_number = evt_write->data[1];
	  if (key_part_number == 0) 
	       memcpy(&unlock_hmac_client[0], &evt_write->data[2], 16);
	  else
	       memcpy(&unlock_hmac_client[16], &evt_write->data[2], 16);
	  app_event.event_type = APP_EVENT_HMAC_PART_RCVD;
	  app_event_queue_add(&app_event_queue, app_event);
     }
}

static void cccd_cfg_out_write_evt(ble_gatts_evt_write_t *evt_write)
{
     struct app_event app_event;
     
     // A subscription is made by the client by writing the characteristic's
     // CCCD (Client Characteristic Configuration Descriptor). A value of 
     // 0x0001 signals a subscription to notifications;
     // 0x0002 signals a subscription to indications. See:
     // See https://www.bluetooth.com/specifications/gatt/
     // viewer?attributeXmlFile=org.bluetooth.descriptor.gatt.
     // client_characteristic_configuration.xml
     if (evt_write->handle == char_handle_cfg_out.cccd_handle) {
	  if (evt_write->data[0] == 0x02 && evt_write->data[1] == 0x00) {
	       app_event.event_type = APP_EVENT_SUBSCRIBED_CFG_OUT;
	       app_event_queue_add(&app_event_queue, app_event);
	  }
     }
}

static void cccd_nonce_write_evt(ble_gatts_evt_write_t *evt_write)
{
     struct app_event app_event;
	  
     // A subscription is made by the client by writing the characteristic's
     // CCCD (Client Characteristic Configuration Descriptor). A value of 
     // 0x0001 signals a subscription to notifications;
     // 0x0002 signals a subscription to indications. See:
     // https://www.bluetooth.com/specifications/gatt/
     // viewer?attributeXmlFile=org.bluetooth.descriptor.gatt.
     // client_characteristic_configuration.xml
     if (evt_write->handle == char_handle_nonce.cccd_handle) {
	  if (evt_write->data[0] == 0x02 && evt_write->data[1] == 0x00) {
	       app_event.event_type = APP_EVENT_SUBSCRIBED_NONCE;
	       app_event_queue_add(&app_event_queue, app_event);
	  }
     }
}

static void on_sys_evt(uint32_t sys_evt)
{
}

static void sys_evt_dispatch(uint32_t sys_evt)
{
    pstorage_sys_event_handler(sys_evt);
    on_sys_evt(sys_evt);
}

static void nonce_indication_hvc_evt(ble_gatts_evt_hvc_t *evt_hvc)
{
     struct app_event app_event;

     if (evt_hvc->handle == char_handle_nonce.value_handle) {
	  app_event.event_type = APP_EVENT_INDICATION_NONCE_RCVD;
	  app_event_queue_add(&app_event_queue, app_event);
     }
}

static void cfg_out_indication_hvc_evt(ble_gatts_evt_hvc_t *evt_hvc)
{
     struct app_event app_event;

     if (evt_hvc->handle == char_handle_cfg_out.value_handle) {
	  app_event.event_type = APP_EVENT_INDICATION_CFG_OUT_RCVD;
	  app_event_queue_add(&app_event_queue, app_event);
     }
}

static void ble_evt_handler(ble_evt_t *ble_evt)
{
     ble_gatts_evt_write_t *evt_write;
     struct app_event app_event;

     switch (ble_evt->header.evt_id) {
     case BLE_GAP_EVT_CONNECTED:
	  conn_handle = ble_evt->evt.gap_evt.conn_handle;
	  app_event.event_type = APP_EVENT_CLIENT_CONNECTED;
	  app_event_queue_add(&app_event_queue, app_event);
	  break;
     case BLE_GAP_EVT_DISCONNECTED:
	  conn_handle = BLE_CONN_HANDLE_INVALID;
	  app_event.event_type = APP_EVENT_CLIENT_DISCONNECTED;
	  app_event_queue_add(&app_event_queue, app_event);
	  break;
     case BLE_GAP_EVT_SEC_PARAMS_REQUEST:
	  // Pairing not supported.
	  sd_ble_gap_sec_params_reply(conn_handle, 
				      BLE_GAP_SEC_STATUS_PAIRING_NOT_SUPP,
				      NULL, NULL);
	  break;
     case BLE_GATTS_EVT_WRITE:
          evt_write = &ble_evt->evt.gatts_evt.params.write;
	  char_cfg_in_write_evt(evt_write);
	  char_unlock_write_evt(evt_write);
	  cccd_cfg_out_write_evt(evt_write);
	  cccd_nonce_write_evt(evt_write);
	  break;
     case BLE_GATTS_EVT_HVC:
	  // Indication has been acknowledged by the client.
	  nonce_indication_hvc_evt(&ble_evt->evt.gatts_evt.params.hvc);
	  cfg_out_indication_hvc_evt(&ble_evt->evt.gatts_evt.params.hvc);
	  break;
     case BLE_GATTS_EVT_SYS_ATTR_MISSING:
	  // No system attributes have been stored.
	  sd_ble_gatts_sys_attr_set(conn_handle, NULL, 0, 0);
	  break;
     case BLE_GAP_EVT_TIMEOUT:
	  // TODO: Should we do something?
	  break;
    }
}

static void ble_stack_init()
{
     // The softdevice uses RTC0 (32 kHz real-time clock) for timing.
     // We use an external crystal with 20 ppm accuracy.
     SOFTDEVICE_HANDLER_INIT(NRF_CLOCK_LFCLKSRC_XTAL_20_PPM, false);

     // Enable BLE stack. 
     ble_enable_params_t ble_enable_params;
     memset(&ble_enable_params, 0, sizeof(ble_enable_params));
     if (sd_ble_enable(&ble_enable_params) != NRF_SUCCESS)
	  die();
     
     // Set Bluetooth address of device.
     ble_gap_addr_t addr;
     if (sd_ble_gap_address_get(&addr) != NRF_SUCCESS)
	  die();
     if (sd_ble_gap_address_set(BLE_GAP_ADDR_CYCLE_MODE_NONE, &addr) !=
	 NRF_SUCCESS)
	  die();
     
     // Subscribe for BLE events.
     if (softdevice_ble_evt_handler_set(ble_evt_handler) != NRF_SUCCESS)
	  die();
     
     // Subscribe for system events (required to dispatch pstorage events)
     if (softdevice_sys_evt_handler_set(sys_evt_dispatch) !=
	 NRF_SUCCESS)
	  die();
}

static void gap_init()
{
     ble_gap_conn_params_t gap_conn_params;
     ble_gap_conn_sec_mode_t sec_mode;

     // Open link, no encryption required on BLE layer. 
     // Security is handled only on the application layer. 
     BLE_GAP_CONN_SEC_MODE_SET_OPEN(&sec_mode);
     
     // Set device name.
     if (sd_ble_gap_device_name_set(&sec_mode,
				    (const uint8_t *) DEVICE_NAME,
				    strlen(DEVICE_NAME)) != NRF_SUCCESS)
	  die();
     
     // Set connection parameters.
     memset(&gap_conn_params, 0, sizeof(gap_conn_params));
     gap_conn_params.min_conn_interval = MIN_CONN_INTERVAL;
     gap_conn_params.max_conn_interval = MAX_CONN_INTERVAL;
     gap_conn_params.slave_latency = SLAVE_LATENCY;
     gap_conn_params.conn_sup_timeout = CONN_SUP_TIMEOUT;     
     if (sd_ble_gap_ppcp_set(&gap_conn_params) != NRF_SUCCESS)
	  die();
}
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
int main(void)
{
     app_state = booting;

     led_init();

     display_init();
     display_on();
     display_text("Booting", 7, NULL, 0);

     timers_init();
     buttons_init();
     lock_init();
     ble_stack_init();
     nonce_init();
     gap_init();
     service_init();
     advertising_init();
     pstore_init();
     app_event_queue_init(&app_event_queue);
	  
     display_text("Ready", 5, NULL, 0);

     // We could trigger a change of connection parameters. However,
     // for the very short interaction between peripheral and central,
     // it might not be worth the effort.
     //conn_params_init();

     // Initialization done. From here on, everything is event-triggered.

     app_state = idle;
     start_button_event_detection();
     start_advertising();

     while (1) {
	  // The following function puts the processor into sleep mode
	  // and waits for interrupts to wake up. Wakeup events include
	  // events from the softdevice, which are processed in the BLE event 
	  // loop, or other events like interrupts from application timers and
	  // pressed buttons.
	  sd_app_evt_wait();

	  // Interrupts create application-level events and put them
	  // into the event queue, which is processed outside the interrupt 
	  // context and with a priority low enough not to block time-critical
	  // operations, e.g., from the softdevice.
	  struct app_event app_event;
	  while (app_event_queue_get(&app_event_queue, &app_event) != -1)
	       state_transition(app_event);
     }
}

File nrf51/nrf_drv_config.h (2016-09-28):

/* Copyright (c) 2015 Nordic Semiconductor. All Rights Reserved.
 *
 * The information contained herein is property of Nordic Semiconductor ASA.
 * Terms and conditions of usage are described in detail in NORDIC
 * SEMICONDUCTOR STANDARD SOFTWARE LICENSE AGREEMENT.
 *
 * Licensees are granted free, non-transferable use of the information. NO
 * WARRANTY of ANY KIND is provided. This heading must NOT be removed from
 * the file.
 *
 */

#ifndef NRF_DRV_CONFIG_H
#define NRF_DRV_CONFIG_H

/* CLOCK */
#define CLOCK_CONFIG_XTAL_FREQ          NRF_CLOCK_XTALFREQ_Default
#define CLOCK_CONFIG_LF_SRC             NRF_CLOCK_LF_SRC_Xtal
#define CLOCK_CONFIG_LF_RC_CAL_INTERVAL RC_2000MS_CALIBRATION_INTERVAL
#define CLOCK_CONFIG_IRQ_PRIORITY       APP_IRQ_PRIORITY_LOW

/* GPIOTE */
#define GPIOTE_ENABLED 1

#if (GPIOTE_ENABLED == 1)
#define GPIOTE_CONFIG_USE_SWI_EGU false
#define GPIOTE_CONFIG_IRQ_PRIORITY APP_IRQ_PRIORITY_LOW
#define GPIOTE_CONFIG_NUM_OF_LOW_POWER_EVENTS 4
#endif

/* TIMER */
#define TIMER0_ENABLED 0

#if (TIMER0_ENABLED == 1)
#define TIMER0_CONFIG_FREQUENCY    NRF_TIMER_FREQ_16MHz
#define TIMER0_CONFIG_MODE         TIMER_MODE_MODE_Timer
#define TIMER0_CONFIG_BIT_WIDTH    TIMER_BITMODE_BITMODE_32Bit
#define TIMER0_CONFIG_IRQ_PRIORITY APP_IRQ_PRIORITY_LOW

#define TIMER0_INSTANCE_INDEX      0
#endif

#define TIMER1_ENABLED 0

#if (TIMER1_ENABLED == 1)
#define TIMER1_CONFIG_FREQUENCY    NRF_TIMER_FREQ_16MHz
#define TIMER1_CONFIG_MODE         TIMER_MODE_MODE_Timer
#define TIMER1_CONFIG_BIT_WIDTH    TIMER_BITMODE_BITMODE_16Bit
#define TIMER1_CONFIG_IRQ_PRIORITY APP_IRQ_PRIORITY_LOW

#define TIMER1_INSTANCE_INDEX      (TIMER0_ENABLED)
#endif
 
#define TIMER2_ENABLED 0

#if (TIMER2_ENABLED == 1)
#define TIMER2_CONFIG_FREQUENCY    NRF_TIMER_FREQ_16MHz
#define TIMER2_CONFIG_MODE         TIMER_MODE_MODE_Timer
#define TIMER2_CONFIG_BIT_WIDTH    TIMER_BITMODE_BITMODE_16Bit
#define TIMER2_CONFIG_IRQ_PRIORITY APP_IRQ_PRIORITY_LOW

#define TIMER2_INSTANCE_INDEX      (TIMER1_ENABLED+TIMER0_ENABLED)
#endif

#define TIMER3_ENABLED 0

#if (TIMER3_ENABLED == 1)
#define TIMER3_CONFIG_FREQUENCY    NRF_TIMER_FREQ_16MHz
#define TIMER3_CONFIG_MODE         TIMER_MODE_MODE_Timer
#define TIMER3_CONFIG_BIT_WIDTH    TIMER_BITMODE_BITMODE_16Bit
#define TIMER3_CONFIG_IRQ_PRIORITY APP_IRQ_PRIORITY_LOW

#define TIMER3_INSTANCE_INDEX      (TIMER2_ENABLED+TIMER1_ENABLED+TIMER0_ENABLED)
#endif

#define TIMER4_ENABLED 0

#if (TIMER4_ENABLED == 1)
#define TIMER4_CONFIG_FREQUENCY    NRF_TIMER_FREQ_16MHz
#define TIMER4_CONFIG_MODE         TIMER_MODE_MODE_Timer
#define TIMER4_CONFIG_BIT_WIDTH    TIMER_BITMODE_BITMODE_16Bit
#define TIMER4_CONFIG_IRQ_PRIORITY APP_IRQ_PRIORITY_LOW

#define TIMER4_INSTANCE_INDEX      (TIMER3_ENABLED+TIMER2_ENABLED+TIMER1_ENABLED+TIMER0_ENABLED)
#endif


#define TIMER_COUNT (TIMER0_ENABLED + TIMER1_ENABLED + TIMER2_ENABLED + TIMER3_ENABLED + TIMER4_ENABLED)

/* RTC */
#define RTC0_ENABLED 0

#if (RTC0_ENABLED == 1)
#define RTC0_CONFIG_FREQUENCY    32678
#define RTC0_CONFIG_IRQ_PRIORITY APP_IRQ_PRIORITY_LOW
#define RTC0_CONFIG_RELIABLE     false

#define RTC0_INSTANCE_INDEX      0
#endif

#define RTC1_ENABLED 0

#if (RTC1_ENABLED == 1)
#define RTC1_CONFIG_FREQUENCY    32768
#define RTC1_CONFIG_IRQ_PRIORITY APP_IRQ_PRIORITY_LOW
#define RTC1_CONFIG_RELIABLE     false

#define RTC1_INSTANCE_INDEX      (RTC0_ENABLED)
#endif

#define RTC_COUNT                (RTC0_ENABLED+RTC1_ENABLED)

#define NRF_MAXIMUM_LATENCY_US 2000

/* RNG */
#define RNG_ENABLED 1

#if (RNG_ENABLED == 1)
#define RNG_CONFIG_ERROR_CORRECTION true
#define RNG_CONFIG_POOL_SIZE        8
#define RNG_CONFIG_IRQ_PRIORITY     APP_IRQ_PRIORITY_LOW
#endif

/* SPI */
#define SPI0_ENABLED 0

#if (SPI0_ENABLED == 1)
#define SPI0_USE_EASY_DMA 0

#define SPI0_CONFIG_SCK_PIN         2
#define SPI0_CONFIG_MOSI_PIN        3
#define SPI0_CONFIG_MISO_PIN        4
#define SPI0_CONFIG_IRQ_PRIORITY    APP_IRQ_PRIORITY_LOW

#define SPI0_INSTANCE_INDEX 0
#endif

#define SPI1_ENABLED 0

#if (SPI1_ENABLED == 1)
#define SPI1_USE_EASY_DMA 0

#define SPI1_CONFIG_SCK_PIN         2
#define SPI1_CONFIG_MOSI_PIN        3
#define SPI1_CONFIG_MISO_PIN        4
#define SPI1_CONFIG_IRQ_PRIORITY    APP_IRQ_PRIORITY_LOW

#define SPI1_INSTANCE_INDEX (SPI0_ENABLED)
#endif

#define SPI2_ENABLED 0

#if (SPI2_ENABLED == 1)
#define SPI2_USE_EASY_DMA 0

#define SPI2_CONFIG_SCK_PIN         2
#define SPI2_CONFIG_MOSI_PIN        3
#define SPI2_CONFIG_MISO_PIN        4
#define SPI2_CONFIG_IRQ_PRIORITY    APP_IRQ_PRIORITY_LOW

#define SPI2_INSTANCE_INDEX (SPI0_ENABLED + SPI1_ENABLED)
#endif

#define SPI_COUNT   (SPI0_ENABLED + SPI1_ENABLED + SPI2_ENABLED)

/* SPIS */
#define SPIS0_ENABLED 0

#if (SPIS0_ENABLED == 1)
#define SPIS0_CONFIG_SCK_PIN         2
#define SPIS0_CONFIG_MOSI_PIN        3
#define SPIS0_CONFIG_MISO_PIN        4
#define SPIS0_CONFIG_IRQ_PRIORITY    APP_IRQ_PRIORITY_LOW

#define SPIS0_INSTANCE_INDEX 0
#endif

#define SPIS1_ENABLED 0
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

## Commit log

2016-09-28 Initial check-in
    [key20-ble.brd, key20-ble.sch, lcd1602a-connector-90deg.brd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]
2016-10-03 Adapted Makefile and code to easily switch between compiling for nRF51 DK and Key20 board.
2016-10-23 Fixed problem when connecting to BLE device after re-enabling Bluetooth adapter
2017-06-10 Fixed bug in key exchange (device not sending correct key number in second part of DH key)
    [key20.c]
